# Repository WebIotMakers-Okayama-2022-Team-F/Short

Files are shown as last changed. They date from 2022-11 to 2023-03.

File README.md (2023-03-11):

# Short
## Discripotion
Smallest Smart Planter / 最小サイズのスマートプランター

この装置は、2022年Web×IoT メイカーズチャレンジPLUSで開発したオープンソースの水耕栽培キットです。<BR>
水耕栽培に必要な水量及び液肥の施肥の制御、気温、水温、照度の記録、LEDライトによる照明の追加、カメラによる成長記録撮影を行うことが出来ます。  
種々の制御やDBへのデータ蓄積、Webツールを使ったデータ可視化を一元的に行うため、制御にはRaspberry Pi 4Bを使用していますが、必要な機能に抑えればESP32などのマイコンを使用しても良いでしょう。  
プロジェクト名「Short」は、一株だけの最小構成の育成用に作ったことを意味しています。栽培する植物や数量に応じてハードを拡張してください。  
基本的な制御にはNode-REDを採用しているため、機能拡張や改良を行う際にも容易にプログラムの修正が可能です。  

## その他資料
Web×IoT メイカーズチャレンジPLUSの公式サイトです。  
https://webiotmakers.github.io/2022/

Web×IoT メイカーズチャレンジPLUSの最終発表時の資料です。  
https://docs.google.com/presentation/d/1nIbv-dXtBHpPwt7HMpmYs73selntcH6rF92BJmyO9pU/edit?usp=sharing

# BOM
## 購入品
|部品|数|備考|
|-|-|-|
|Raspberry Pi 4B|1||
|Raspberry Pi Camera V2.1|1||
|BH1750|1|照度センサ|
|SHT30|1|温湿度センサ|
|NeoPixel x 12 Ring|1|照明|
|NeoPixel x 16 Ring|1|照明|
|NeoPixel x 24 Ring|1|照明|
|土壌水分センサ|1|改造して水位センサとして使用|
|ねじ|いろいろ、後でまとめる||
|スペーサ|いろいろ、あとでまとめる||
|USB TypeC male to female cable|1|電源延長用|
|Wi-Fi USBドングル|1|Wi-Fi APとして運用する場合|
|φ8真鍮線 300mm|1|改造水位センサ用|
|エポキシ接着材|1|100円ショップのやつでOK　解像水位センサ用|
|方軸TTモーター|2|ポンプ駆動用|
|シリコーンゴムチューブ I.D.2×O.D.3×50cm|1|ポンプ用|
|ベアリング I.D.4×O.D.7×2.5t|16|ポンプ用|
|DRV8833モータードライバボード|1|ポンプ制御用|
|2N2222トランジスタ|1|ポンプ制御用|
|ユニバーサル基盤|2|コネクタ分配用|
|PH2.0コネクタ male 2Pin|3||
|PH2.0コネクタ female 2Pin|3||
|PH2.0コネクタ male 3Pin|1||
|PH2.0コネクタ female 3Pin|1||
|PH2.0コネクタ male 4Pin|4||
|PH2.0コネクタ female 4Pin|4||
|PH2.0コネクタ male 6Pin|2||
|PH2.0コネクタ female 6Pin|2||
|AWG26 SR被覆 ソフトワイヤ|適量||
|Dupont Pin Socket|適量||
||||
||||

# 3D Printer Parts
|パーツ名|数|備考|
|-|-|-|
|base|1|ベース|
|bottom for main tank|1|メインタンクを使用する場合の底パーツ|
|frame side layout|1|フレーム|
|frame cover|1|フレームカバー|
|main tank|1|メインタンク|
|port cover|1|Raspberry PiのUSBポートカバー|
|pot|1|栽培ポット|
|pot cover|1|main tank の上にpotを載せるカバー|
|LED blacket|1|LED、カメラを取り付けるブラケット|
|top cover|1|天面カバー|
|level sensor bracket|1|水位センサーのブラケット|
|pump_pulseless_core_for_chinaa tube|1|チューブポンプのローター|
|pump_pulseless_cover|1|チューブポンプのローターカバー|
|pump_pulseless_vertical|1|縦置き型チューブポンプケース|

# Instllation
## Hardware Assy

## Software
Raspberry PiのOS及び必要なソフト類をインストールしてください。<BR>
必要とする環境は次の通りです。<BR>

  Raspberry Pi OS Legacy 32bit(buster)
  Python3
  OpenCV
  Node-RED
  Web-I2C-API
  MariaDB
  Grafana

### Raspberry Pi Setup
Raspberry Piはlegacyの32bit版を使用します。<BR>
Raspberry Pi Imagerを使用し、以下のOSを選択して起動用MicroSDカードを作成してください。<BR>
「OSを選ぶ」⇒「Raspberry Pi OS(other)」⇒Raspberry Pi OS(Legacy)<BR><BR>
<BR>
使用しているOSはlsb_releaseコマンドで確認できます。<BR>
```
$ lsb_release -a
No LSB modules are available.
Distributor ID:	Raspbian
Description:	Raspbian GNU/Linux 10 (buster)
Release:	10
Codename:	buster
```

続いて、各種設定を行います。
次のコマンドでraspi-configを起動してください。
```
sudo raspi-config
```

カメラを有効化します。<BR>
[3 Interface Options]->[P1 Camera]->[<はい>]<BR>
SSHを有効化します。<BR>
[3 Interface Options]->[P2 SSH]->[<はい>]<BR>
VNCを有効化します。<BR>
[3 Interface Options]->[P3 VNC]->[<はい>]<BR>
I2Cを有効化します。<BR>
[3 Interface Options]->[P5 I2C]->[<はい>]<BR>

### Web I2C API instllation
このシステムではセンサ駆動に一部のセンサ駆動にWeb I2C APIを使用しています。Node-REDから直接センサを駆動する場合は不要です。<BR>

作業フォルダを作成してnpmとWeb-I2c-APIをインストールします。<BR>
```
mkdir Workspace
cd Workspace
npm init -y
npm install node-web-gpio node-web-i2c
```

合せてセンサを動かすためのライブラリもダウンロードします。
```
cd $HOME
wget https://github.com/chirimen-oh/chirimen/archive/refs/heads/master.zip
unzip master.zip
mv chirimen-master/ chirimen/
```

### Node-RED installation
今回はNode-REDでデバイスの操作を統合します。<BR>
次のコマンドでインストールできます。<BR>
```
bash <(curl -sL https://raw.githubusercontent.com/node-red/linux-installers/master/deb/update-nodejs-and-nodered)
```

再起動時にも自動的にNode-REDが起動するようにします。<BR>
```
sudo systemctl enable nodered.service
```
詳しくは公式サイトをご確認下さい。<BR>
https://nodered.jp/docs/getting-started/raspberrypi

### MariaDB installation
集めたデータはMariaDBというMySQL互換のデータベースに蓄積します。<BR>
MariaDBのインストール方法はQiitaにまとめていますのでこちらを参考にしてください。<BR>
https://qiita.com/airpocket/items/f1dd8e0d32be6075b7de<BR>

### Grafana installation
GrafanaをRPiへインストールする方法は[公式サイトで説明されています](https://grafana.com/tutorials/install-grafana-on-raspberry-pi/)のでこの通りに進めていきます。<BR>

パッケージの認証に使用されるAPTキーを追加する。<BR>

```sh
wget -q -O - https://packages.grafana.com/gpg.key | sudo apt-key add -
```

GrafanaAPTリポジトリを追加する。<BR>

```sh
echo "deb https://packages.grafana.com/oss/deb stable main" | sudo tee -a /etc/apt/sources.list.d/grafana.list
```

Grafanaをインストールする。<BR>

```sh
sudo apt-get update
sudo apt-get install -y grafana
```

Grafanaサーバーを有効にする。<BR>

```sh
sudo /bin/systemctl enable grafana-server
```

Grafanaサーバーを起動する。<BR>

```sh
sudo /bin/systemctl start grafana-server
```

以上でRPi上でGrafanaが動き始めました。<BR>

### OpenCV installation
```
sudo pip3 install opencv-python
sudo apt-get install libatlas-base-dev
sudo pip3 install numpy --upgrade
``` 

### MariaDBにデータベースを作成する<BR>
MariaDBに、必要なデータベースを作成します。作成する方法にはRaspberry Pi上から直接SQL言語を使用する方法と、他のWindowsPCなどからGUIツールを使って作成する方法があります。HeidiSQLというツールを使用する方法が簡単ですので以下のページに方法をまとめています。<BR>
https://qiita.com/airpocket/items/5e73444459b7ad5b0666
<BR>
作成するデータベースは次の構成にします。<BR>
データベース名<BR>

### Node-REDでセンサを制御し、データベースへ書き込む
  Node-REDのプログラムはこちらを参照してください。
  次のノードが必要ですので事前にパレットに追加してください。
  
  node-red-contrib-ads1x15_i2c<BR>
  node-red-contrib-aedes<BR>
  node-red-contrib-bh1750<BR>
  node-red-contrib-sht<BR>
  node-red-contrib-dashboard<BR>
  node-red-node-mysql<BR>
  node-red-node-pi-gpio<BR>
  node-red-pi-neopixel<BR>

### Grafanaで可視化
  Grafanaでデータを可視化する方法は次の記事にまとめています。
  https://qiita.com/airpocket/items/61209b40f0cddf8f90ed

# license
"Smart Planter Short" by WebIoTMakers Okayama 2022 Team Farmer is licensed underCC BYSA 2.0

<br />この 作品 は <a rel="license" href="http://creativecommons.org/licenses/by-sa/4.0/">クリエイティブ・コモンズ 表示 - 継承 4.0 国際 ライセンス</a>の下に提供されています。

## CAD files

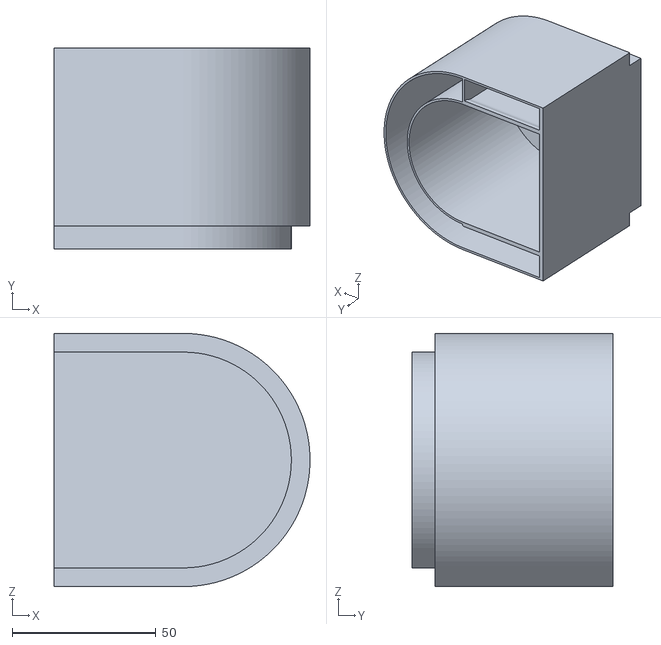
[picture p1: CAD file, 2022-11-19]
stl/main tank v3.stl
89.0 x 70.0 x 88.0

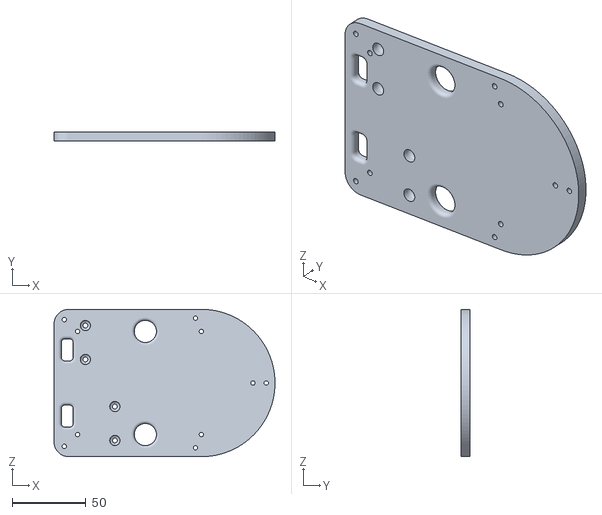
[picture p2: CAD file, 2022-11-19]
stl/bottom for main tank v2.stl
150.0 x 6.00 x 100.0

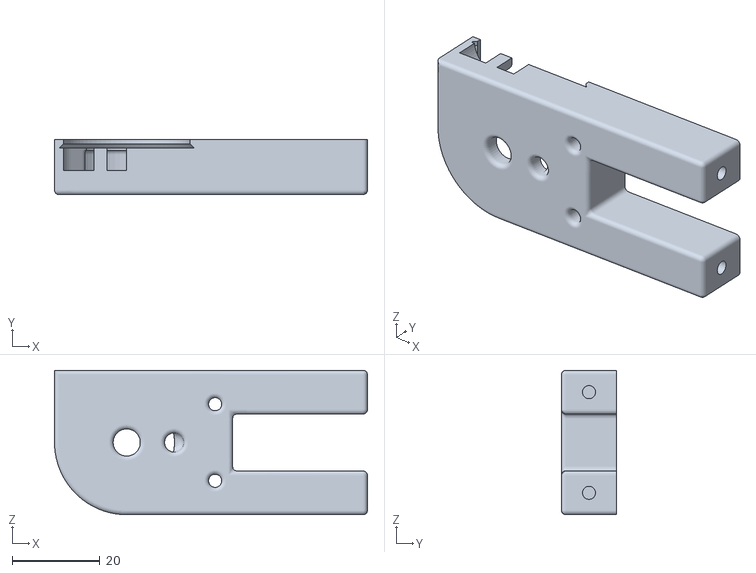
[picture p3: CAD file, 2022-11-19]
stl/pump_pulseless v6.stl
71.5 x 12.6 x 33.0

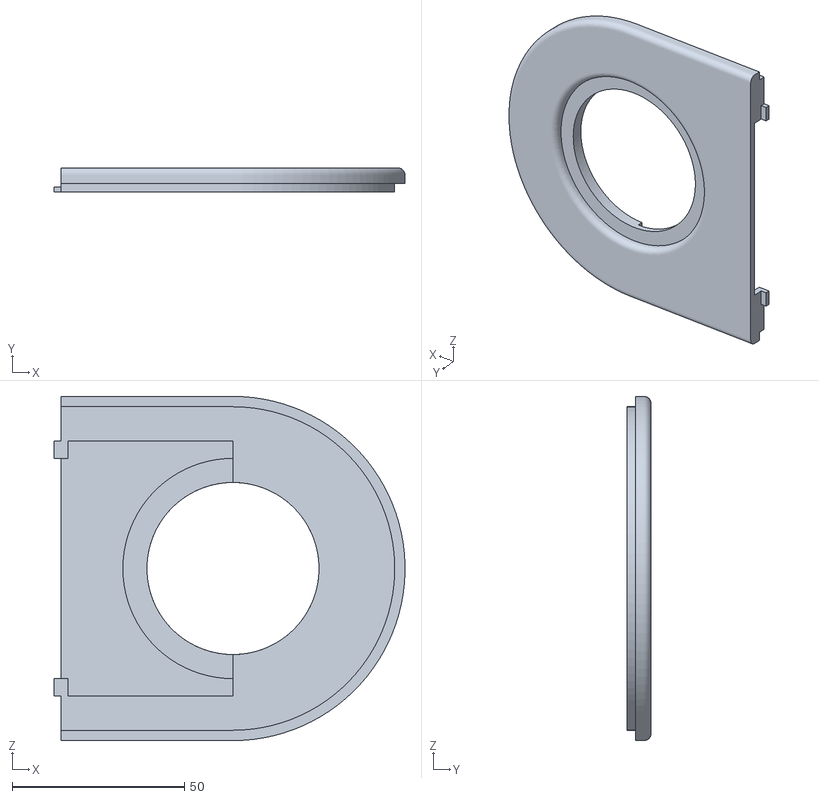
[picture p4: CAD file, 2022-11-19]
stl/pot cover v6.stl
102.0 x 7.00 x 100.0

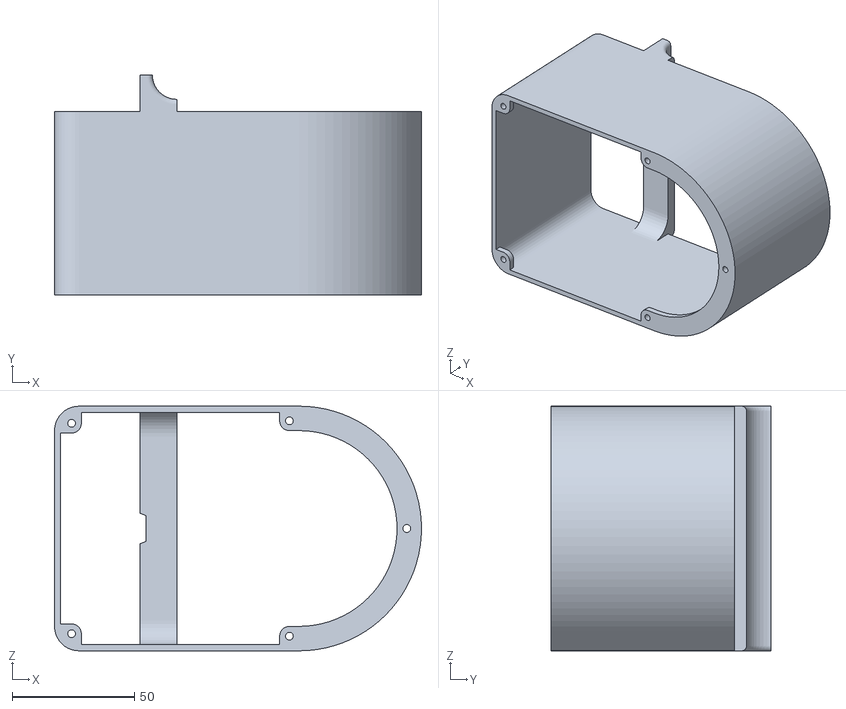
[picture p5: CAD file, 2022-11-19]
stl/planter base v6.stl
150.0 x 90.0 x 100.0

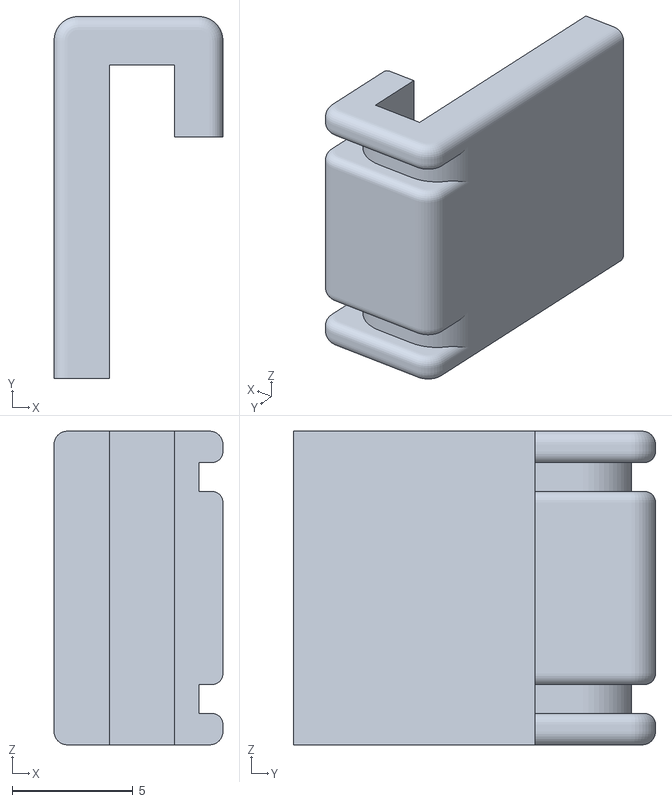
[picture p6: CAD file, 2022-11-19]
stl/level sensor bracket v3.stl
7.00 x 15.0 x 13.0

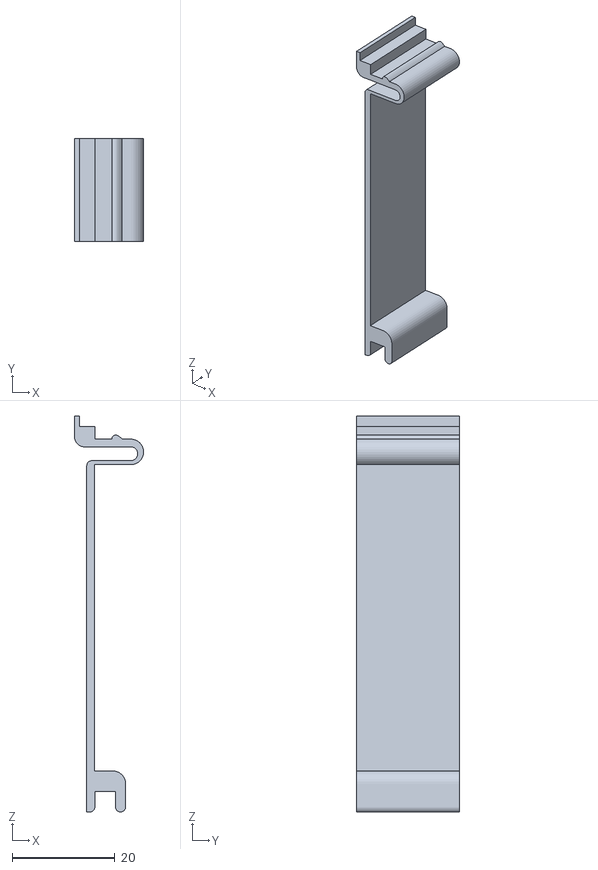
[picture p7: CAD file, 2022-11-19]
stl/port cover v8.stl
13.5 x 20.0 x 77.2

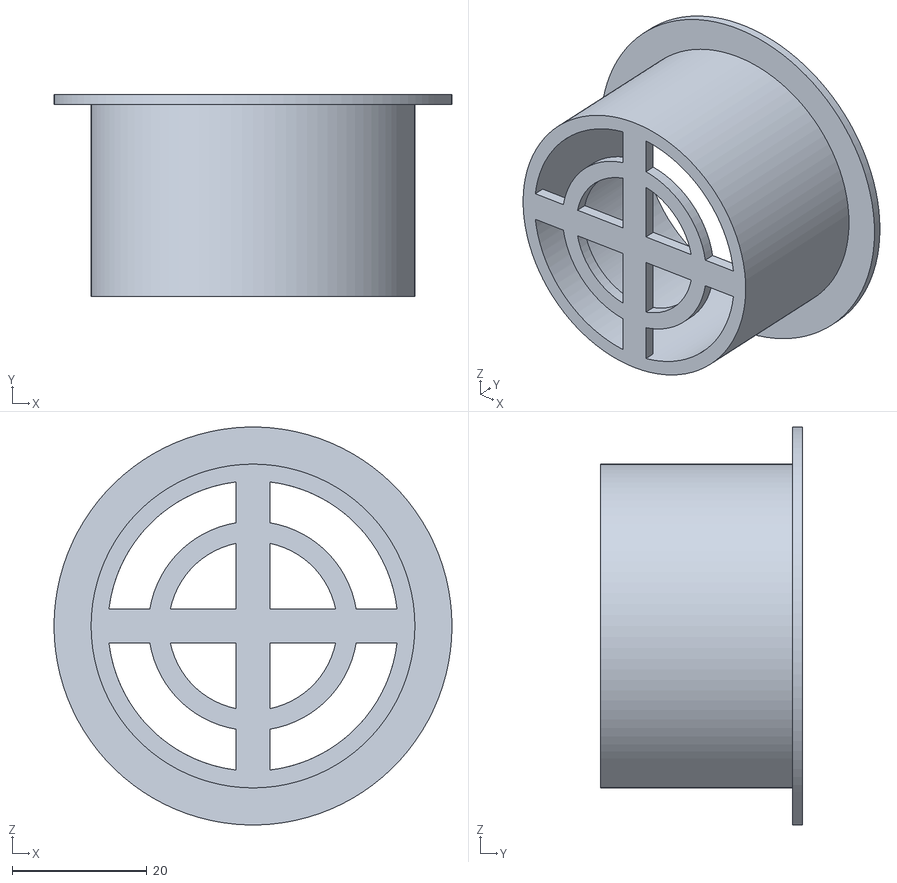
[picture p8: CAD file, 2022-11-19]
stl/pot v4.stl
59.0 x 30.0 x 59.0

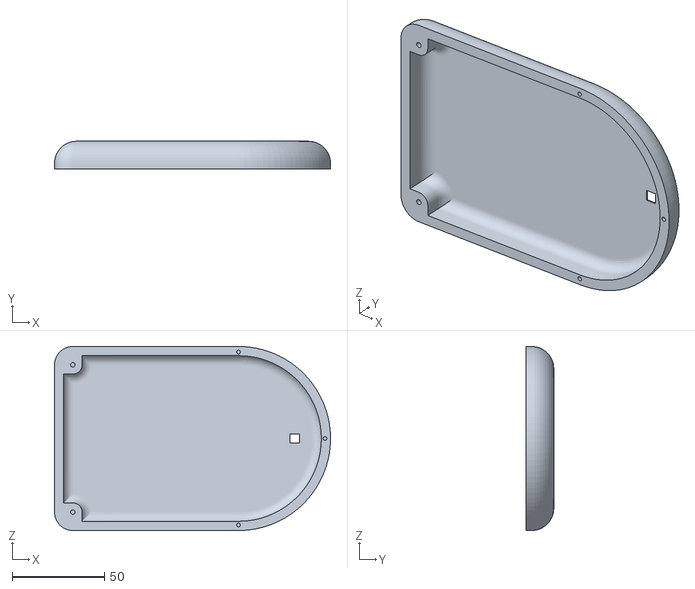
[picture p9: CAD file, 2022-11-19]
stl/top cover v1.stl
150.0 x 15.0 x 100.0

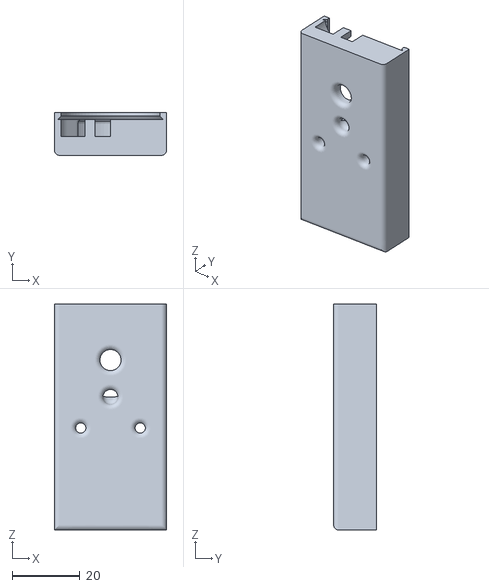
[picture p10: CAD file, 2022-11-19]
stl/pump_pulseless_vertical v3.stl
33.0 x 12.6 x 66.5

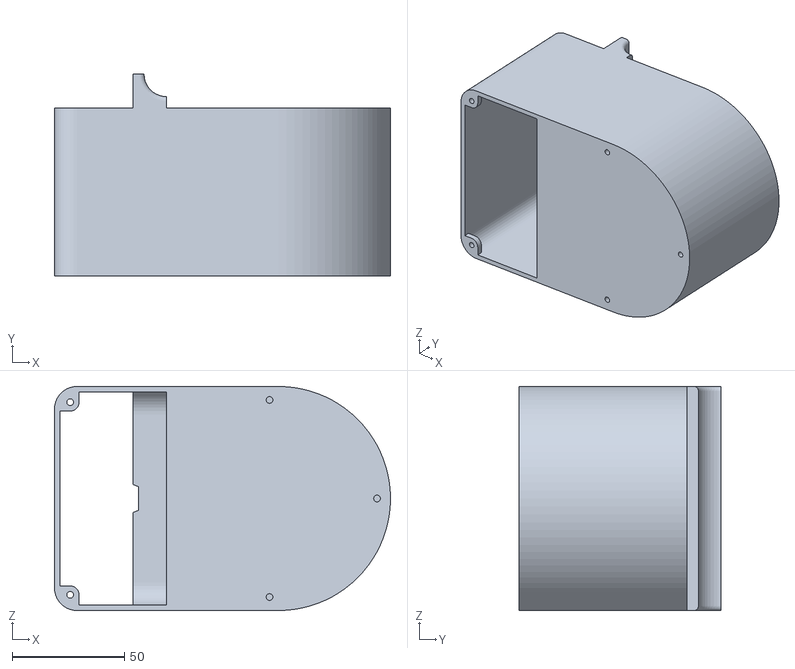
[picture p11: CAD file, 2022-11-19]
stl/planter base2 v1.stl
150.0 x 90.0 x 100.0

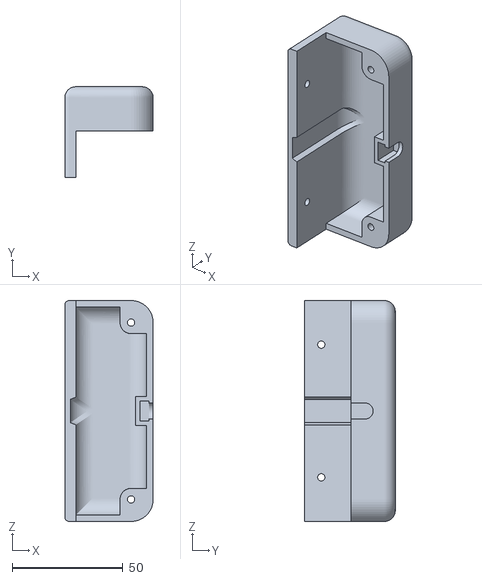
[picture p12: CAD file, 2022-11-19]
stl/top rover v2.stl
40.0 x 41.0 x 100.0

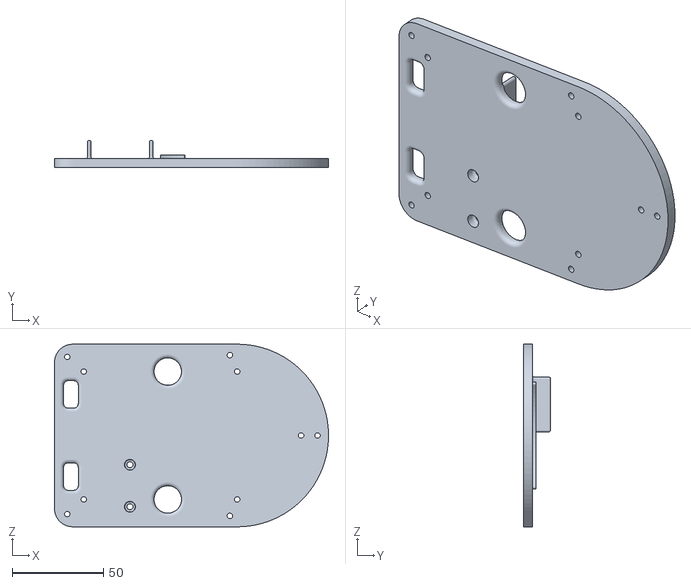
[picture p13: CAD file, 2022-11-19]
stl/bottom v8.stl
150.0 x 15.0 x 100.0

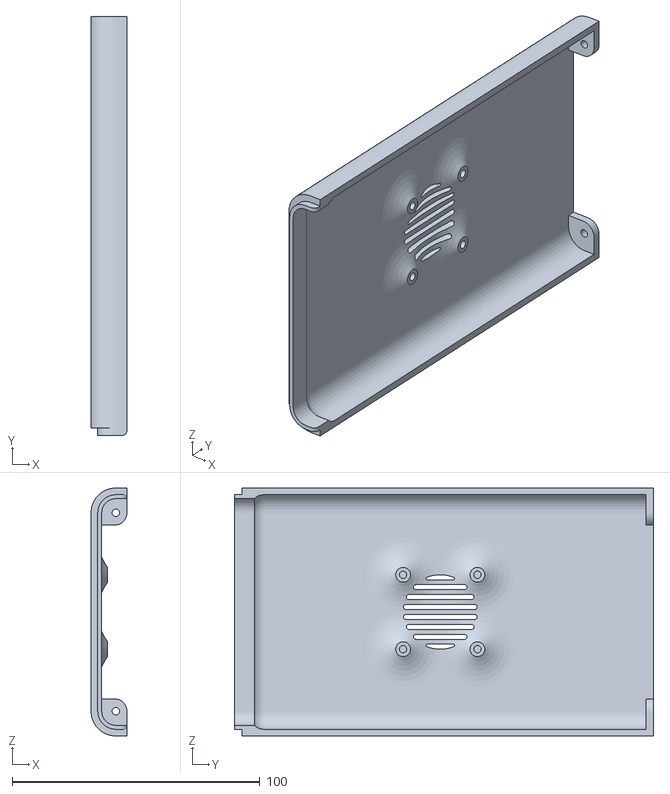
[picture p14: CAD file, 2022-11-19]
stl/frame cover v4.stl
14.5 x 169.0 x 100.0

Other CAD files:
stl/pump_pulseless_core_for china tube v1.stl
stl/frame v8.stl
stl/rover bumper v2.stl
stl/base v15.stl
design/fusino360/LED blacket v15.f3d
design/fusino360/base v15.f3d
design/fusino360/frame v7.f3d
design/fusino360/planter base v6.f3d
design/fusino360/pot cover v5.f3d
design/fusino360/pot v3.f3d
stl/LED blacket v17.stl
stl/frame side layout v4.stl
stl/pump_pulseless_cover_Re v1 v1.stl
stl/rover base v1.stl

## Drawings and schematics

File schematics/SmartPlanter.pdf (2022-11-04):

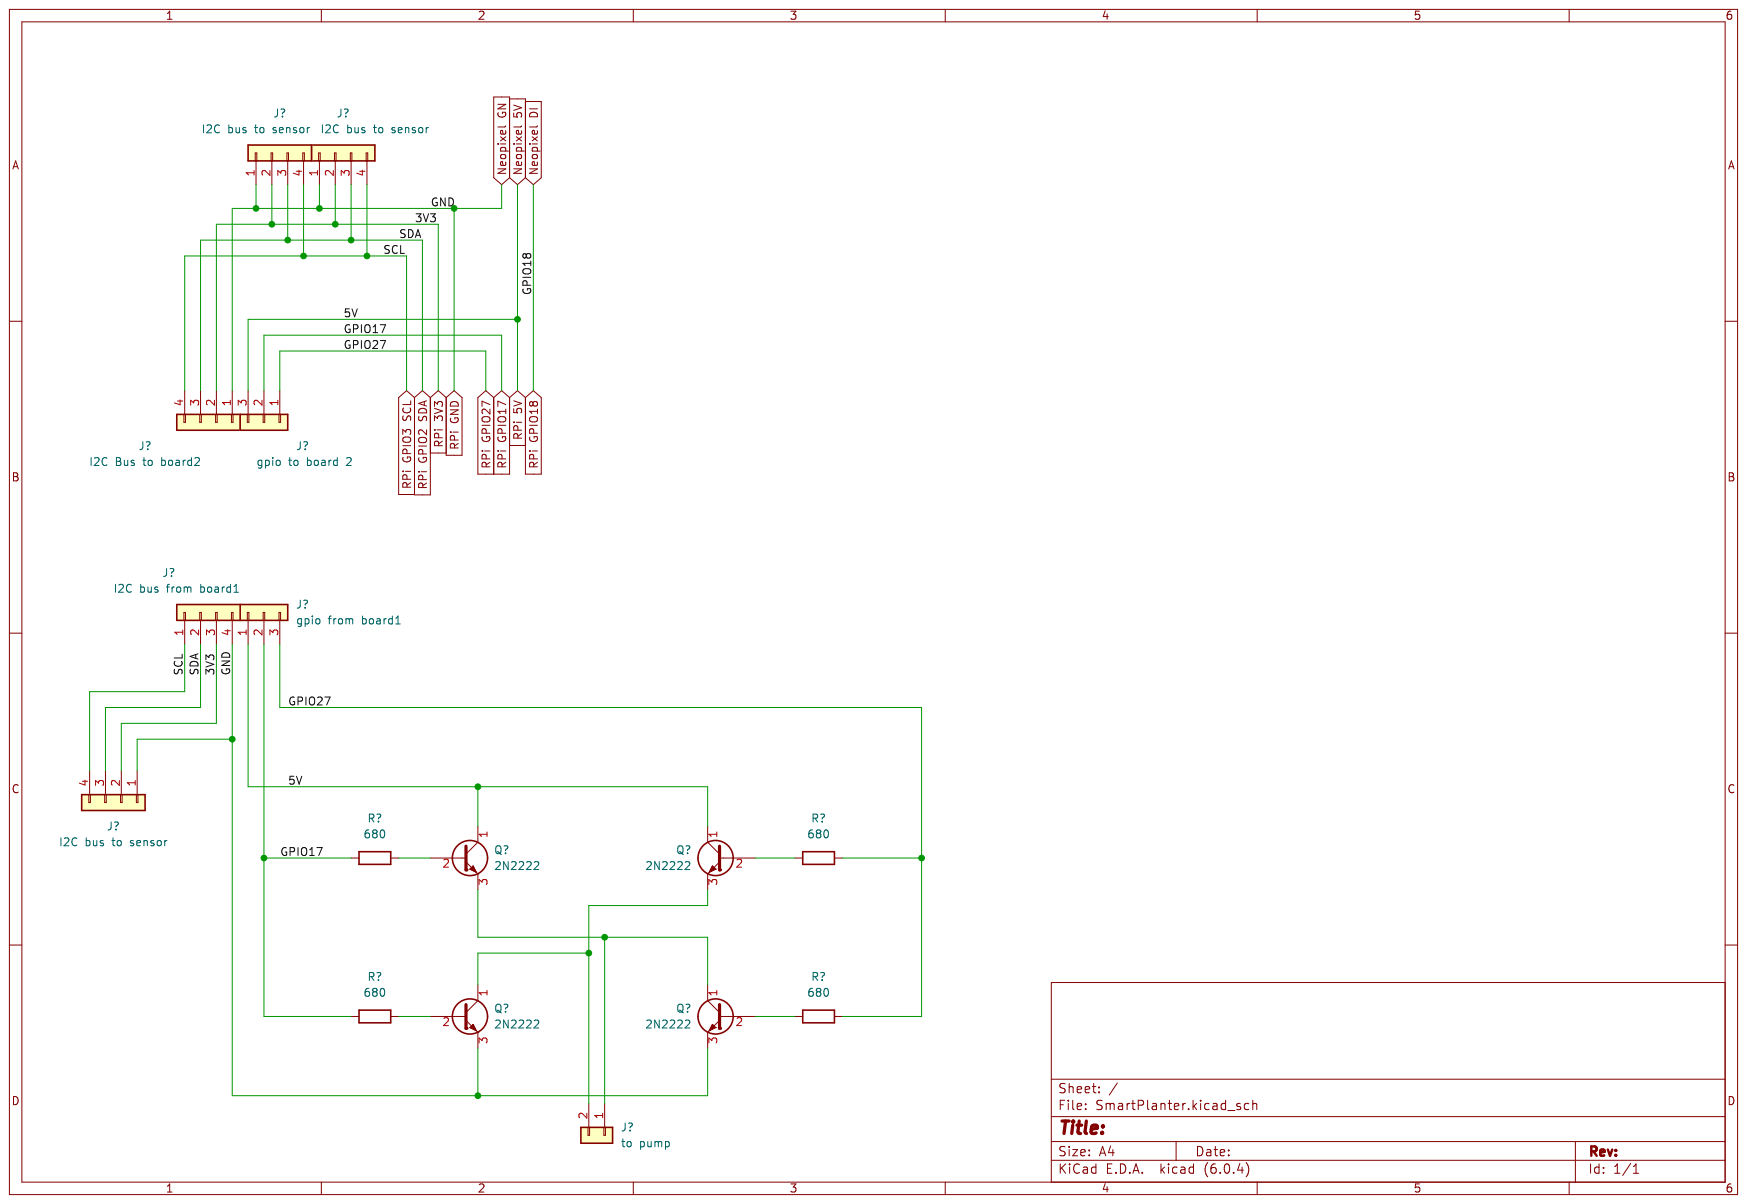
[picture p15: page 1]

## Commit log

2022-10-13 Add files via upload
    first
    [LED blacket v15.f3d, base v15.f3d, frame v7.f3d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]
2023-03-11 Update README.md
    Node-RED の追加ノードを記載
